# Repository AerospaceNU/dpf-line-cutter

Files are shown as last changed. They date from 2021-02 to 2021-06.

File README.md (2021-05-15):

# Line Cutter: For Cutting Lines
The line cutter is a system for deploying a single parachute as both drogue and main. Reefing lines are used to constrict the parachute to two intermediate sizes, and these lines are threaded through line cutters. At the set altitudes (or after a time delay), nichrome wires burn through the reefing lines.

## Organization
* `code`: Line cutter code and flight data analyses.
  * `launch archive`: Raw flight data and summaries of successes/failures from past line cutter flights. Subfolders should be named with ISO date and launch site.
  * `libraries and drivers`: Should be obsolete soon (drivers etc. will be published as Arduino libraries).
    * `openocd_windows.zip`: Windows build of openOCD with nrf52940 bootloader and cheap st-link config packaged.
  * `tests`: Code that is useful for testing various line cutter features across hardware versions.
  * `v1`: Code for v1 perfboard line cutters.
  * `v2`: Code for mixed perfboard and PCB line cutters.
  * `v3`: Code for current PCB line cutters.
    * `bulk_erase`: Erases all data on flash chip.
    * `flash_reader`: Reads all data on flash chip.
    * `flight_variable_upload`: Sets parameters for flight.
    * `identifier`: Names PCB for Bluetooth advertising.
    * `InternalFS_format`: Erases files on NRF52840 and formats filesystem.
    * `line_cutter_v3`: Main program that runs on flights.
    * `memory_reader`: Reads state transition log.
* `docs`: More detailed documentation, see below for list.
* `schematic`: ECAD files for the line cutter hardware. Contains schematics for all line cutter hardware. Folder structure is described in the [readme](schematic/README.md)

## Documentation
Code documentation applies to the latest version (v1/v2 are not compatible with current line cutters).
* [`CHECKLIST`](docs/CHECKLIST.md): Pre-flight checklist for line cutter launches.
* [`FLASH`](docs/FLASH.md): Procedure for logging data to flash on line cutters.
* [`SIGNALS`](docs/SIGNALS.md): Description of current board.
* [`STATES`](docs/STATES.md): Description of state machine.
* [`nrf52_openocd`](docs/nrf52_openocd.md): Instructions for programming NRF52 chips with OpenOCD.

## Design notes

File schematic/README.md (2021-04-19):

# Line cutter schematics

This folder is organized as follows:
  * `batt-and-reg.cam`: CAM file used for JLC
  * `lineCutterR<N>-.zip`: Production files sent to fab
  * `LineCutter`: eagle project containing all the actual files
    * `Line Cutter COTS.lbr`: common parts used (flash memory, nRF daughterboards, etc)
    * `lineCutterR1`: first PCB ordered (nRF52832, December 2020)
    * `lineCutterR2`: ESP32-S2 based, ordered spring 2021 (1 built, no software written for it)
    * `lineCutterR3`: nRF52840-based, ordered spring 2021. Flew Amesbury 3/20.

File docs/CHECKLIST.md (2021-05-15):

This is the pre-flight checklist that should be followed for every line cutter launch. Detailed instructions for setting up the line cutters are elsewhere; read those first. Consider any time limits mentioned to be a lower bound---completing items *earlier* than the listed time is encouraged, *on-time* is acceptable, and *after* will result in a rushed (read: risky) process. Keep in mind that although the checklist only covers line cutter prep, it implicitly requires that the rest of your rocket is also prepared in a timely manner.

14 days before launch:
- [ ] Ensure that you have all materials needed for setup (if you need to ship more stuff, it's important to know this early)

6 days before launch:
- [ ] Sew outer cases and loops onto your parachute
- [ ] Make a local copy of the `dpf-line-cutter` repository

3 days before launch:
- [ ] Assemble the cases (including nichrome)
- [ ] Decide on reefing amounts and reef the parachute
- [ ] Ejection test with the assembled cases

1 day before launch:
- [ ] Charge all batteries (and spares)
- [ ] Put your PCBs in the cases
- [ ] Erase the flash memory on the PCBs
- [ ] Decide on and upload flight variables
- [ ] Upload flight code

On launch day:
- [ ] Plug in the batteries once you have a reasonable expectation that the PCBs won't run out of memory (< 3 hours before launch)
- [ ] Immediately use `!vars` and `!data` to check for expected values from both line cutters
- [ ] Put (preferably black) etape over LEDs
- [ ] Burrito your parachute and put in your rocket, but don't screw things together yet
- [ ] Use `!data` to check that the photoresistors are reading below ~200 on both line cutters
- [ ] Finish assembling rocket

On the rail:
- [ ] Use `!data` for final confirmation that photoresistors are reading below ~200 and state is `WAITING` on both line cutters
- [ ] Arm both line cutters with `!arm`
- [ ] Use `!data` to confirm that both line cutters are in the `ARMED` state
- [ ] *Optional: if the rocket needs to be taken off the rail for any reason, you should `!disarm` both line cutters and confirm using `!data`*
- [ ] Launch!

After landing:
- [ ] Take photos of both line cutters when you recover your rocket
- [ ] Visually confirm that both lines have disreefed
- [ ] Once you're back at the lab, follow the flash offload instructions to get flight data
- [ ] Send data to the line cutter team
- [ ] Report any potential issues with or damage to the individual line cutters
- [ ] Disassemble and return components

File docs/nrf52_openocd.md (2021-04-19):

# Programming NRF52 chips with OpenOCD

## With ST-Link

St-link V2s can be had for as little as $5, and work on Windows or Linux. A Windows build of OpenOCD, along with config file for the nrf52, is in `code/libraries and drivers/openocd_windows.zip`.

## With a Pi 3ish

Diagrams taken from [here](https://iosoft.blog/2019/01/28/raspberry-pi-openocd/) -- the Medium article went poof but we have the [Internet Archive](https://web.archive.org/web/20191204234928/https://medium.com/@ly.lee/coding-nrf52-with-rust-and-apache-mynewt-on-visual-studio-code-9521bcba6004) for that.

Wire the nRF52 to a Pi 2+ with the following:

```
GND -> GND
SWDIO/TMS -> Physical pin 18 (BCM 24)
SWCLK/TCK -> Physical pin 22 (BCM 25)
nRESET -> Phsyical pin 12
```

Note that the 3v3 rail on the Pi gets sad when you plug a whole Feather in. I'd suggest powering it externally.

Flash a Pi with Raspbian. You'll likely want one with a desktop environment so you can register with Resnet.

Install OpenOCD with `sudo apt update && sudo apt install openocd`

Create a file `bcm-nrf.cfg` with the following:

```
# Use RPi GPIO pins
interface bcm2835gpio

# Base address of I/O port
bcm2835gpio_peripheral_base 0x3F000000

# Clock scaling
bcm2835gpio_speed_coeffs 146203 36

# SWD                swclk swdio
# Header pin numbers 22    18    (counting from 1 on the top left)
bcm2835gpio_swd_nums 25    24

transport select swd

source [find target/nrf52.cfg]

# gdb_breakpoint_override hard
```

Run `sudo openocd -f bcm-nrf.cfg`. This should produce something that looks like this:

```
Open On-Chip Debugger 0.11.0-rc2+dev-00001-g5c17ce508-dirty (2021-01-27-17:38)
Licensed under GNU GPL v2
For bug reports, read
        http://openocd.org/doc/doxygen/bugs.html
DEPRECATED! use 'adapter driver' not 'interface'
Info : Listening on port 6666 for tcl connections
Info : Listening on port 4444 for telnet connections
Info : BCM2835 GPIO JTAG/SWD bitbang driver
Info : clock speed 1001 kHz
Info : SWD DPIDR 0x2ba01477
Info : nrf52.cpu: hardware has 6 breakpoints, 4 watchpoints
Info : starting gdb server for nrf52.cpu on 3333
Info : Listening on port 3333 for gdb connections
```

If you see something that starts with `Error:`, check your connections and try again.

## Flashing Bootloader

Connect with `telnet localhost 4444`. You may need to `sudo apt install telnet` (Linux) or enable the telnet clilent (Windows) first.

We will use the Adafruit bootloader from [here](https://github.com/adafruit/Adafruit_nRF52_Arduino/tree/master/bootloader). A copy is in `code/libraries and drivers/nrf52840_express.hex`. Transfer it to the Pi and run the following command in OpenOCD.

```
reset init
halt
nrf5 mass_erase
program <full/path/to/bootloader.hex> verify
reset
```

Note that you must call `reset` for the board to enumerate. To erase all:

```
nrf52.dap apreg 1 0x04 0x01
nrf52.dap apreg 1 0x04 // This should be 0x01
```

Now the nRF52 can be connected over USB and programmed with the Arduino IDE.

<!-- pi@raspberrypi3:~ $ sudo openocd -f interface/raspberrypi2-native.cfg -c "transport select swd" -f target/nrf52.cfg -d2 -c init -c "reset init" -c halt -c "nrf5 mass_erase" -c "program espruino.hex verify" -c reset -c exit -->

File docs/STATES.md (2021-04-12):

# Line Cutter State Machine

The line cutter uses a simple progression of states. With the exception of the first two states (`waiting` and `armed`), which can be visited multiple times, the states advance in a linear manner.

| State | Requirement | Next state |
|---| --- | --- |
| `waiting` | Receive `!arm` signal from BLE central. | `armed ` |
| `armed` | Receive `!disarm` signal from BLE central. <br> Photoresistor detects bright light.| `waiting` <br> `deployed` |
| `deployed` | Altitude goes below first disreef height. | `partial disreef` |
| `partial disreef` | Altitude goes below second disreef height. | `full disreef` |
| `full disreef` | Speed is below landing limit speed. | `landed` |
| `landed` | N/A | N/A |

## Transitions

All state transitions add data to a state transition log on the NRF52 chip. In addition, some transitions execute special actions first.

* `armed` -> `deployed`: Existing state transition log is deleted.
* `deployed` -> `partial disreef`: PWM begins on first nichrome pin.
* `partial disreef` -> `full disreef`: PWM begins on second nichrome pin.

The PWM on each nichrome pin is started during a state transition, and the time of this transition is marked. Once the defined PWM duration has passed since the transition, the PWM will end.

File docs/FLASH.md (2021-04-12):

# Flash procedure
The line cutter has 16MiB of flash memory divided into 64 sectors of 256kiB each. The first sector is reserved for metadata, including flight variables and a record of which sectors have been written to.

## Writing metadata
Since there are 64 sectors, the first 64 bytes are used to keep track of which sectors are not empty. The rest of the first sector is used for other metadata such as flight information. When a line cutter is turned on, it will use the first 64 bytes to determine the last non-empty sector. Then, it will conduct a linear search of this sector to find the first location with no data, and pick up logging data at that location. When the current sector fills up, the next byte of location metadata is updated. The main advantages of this system are that there are no sector erases (which take ~500ms, or 10 missed data points), and that if a line cutter restarts it is fairly simple to find the first empty flash location.

The line cutter currently logs 64B of data at 20 Hz. At this rate, about 3.5 hours of data can be recorded. After the flash is full, no more data is logged. Leading up to a launch, the flash should be bulk erased before the main program is uploaded, after which the line cutter should be connected to power as little as possible to make sure it doesn't run out of memory.

## Flash contents
| Address (start -> end) | Contents |
| ---| --- |
| 0000000h -> 000003Fh | Whether the corresponding sector is empty. |
| 0000040h -> 003FFFFh | Additional metadata. |
| 0040000h -> 0FFFFFFh | Flight data. |

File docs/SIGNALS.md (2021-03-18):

# Signals

The following signals are connected to the following pins on the nRF module, which correlate to the following Arduino pins on the [Adafruit core](https://github.com/adafruit/Adafruit_nRF52_Arduino/blob/master/variants/feather_nrf52840_express/variant.cpp). Analog pins are listed along with their digital equivilants.

| Description | Physical pin(s) | Arduino pin(s) | Uses | Driver |
| ----- | --- | --- | --- | --- |
| I2c SCL/SDA | P0.11/P0.12 | 22/23 | [Barometer](https://www.digikey.com/en/products/detail/te-connectivity-measurement-specialties/MS560702BA03-50/4700921), [Accelerometer](https://www.digikey.com/en/products/detail/tdk-invensense/ICM-20602/5872870) | Modified MS5xxx, Need to write one |
| SPI MISO/MOSI/SCK/CS0 | P0.15, P0.13, P0.14, P0.16 | 25, 25, 26, 8 | Flash memory | [S25FLx](https://github.com/BleepLabs/S25FLx) |
| SWDIO/SWDCLK | SWDIO/SWDCLK | | Used to program the chip (initially), debugging | |
| BATT_SENSE | P0.02 | A4 (18) | Battery voltage divider | Battery voltage = 2 * (analogRead(A4) / analogReadResolution) |
| CUT_SENSE1/2 | P0.03/0.04 | A5/A0 (19/14)  | Nichrome continuity | Should read about half of Vbatt when connected |
| V_CURR_SENSE | P0.05 | A1 (15) | [Current sense IC](https://www.digikey.com/en/products/detail/allegro-microsystems/ACS711KEXLT-15AB-T/3868192) | The output rises by 90mV / Amp, centered around VCC/2. We should figure out how to read Vcc |
| PHOTO- | P0.28 | A3 (17) | Output of the photoresistor voltage divider |
| CUT1/2 | P0.06/0.08 | 11, 12 | MOSFETs for nichrome |
| RESET | P0.18 | Not Usable | Reset button |
| UART RXD/TXD | P0.24/P0.25 | 1, 0 | UART (Not used currently) |
| USER LED | P1.10 | 4 (PIN_LED2) | Lefmost LED ("blue" LED on feathers). By default blinks for Bluetooth connection |
| RGB LED | P0.17, P0.19, P0.20 | 29, 27, 28 | Red, Green, Blue, respectively |

# Things to check before plugging a board in

- Resistance between ground and:
  - 3v3 (header)
  - VBUS (from the USB, header)
  - VBAT
  - SCL/SDA (should be open -- short will cause sketch to hang)

- Resistance between 3v3 and:
  - SCL/SDA (4.7k pullup expected)

# Places to watch out for

- Accelerometer -- Can't see shorts
- nRF -- can't see solder joints, and reflowing after oven will likely kill it

# Board names

| Board Number | Name | Known Issues |
| ----- | --- | --- |
| 1 | 0Strawberry | |
| 2 | 0Cherry | |
| 3 | 0Did you ever hear the tragedy of Darth Plagueis the Wise? | |
| 4 | 0Apple | |

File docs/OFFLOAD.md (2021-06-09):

# Summary
This document explains how to offload data from the line cutters' flash memory. It will also go over proper folder organization for commits of data to the repository.

# Setup
You should already have a local version of this repo as part of the general preparation for a line cutter flight. In addition, download [CoolTerm](https://freeware.the-meiers.org/), which will be used to save data from the Arduino serial monitor.

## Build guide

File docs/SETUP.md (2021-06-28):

# Line Cutter Setup
blah blah
## Table of Contents
- Materials
- Sew cases and loops
- Assemble cases (with nichrome and PCBs)
- Choose reefing diameters and flight variables
- Upload code
- Use BluefruitConnect
- Pack the parachute
- Steps after launch

## Materials
- 2 line cutter PCBs
- 2 line cutter cases
- 2-56 screws
	- 6 x 1/2"
	- 8 x 3/16" (1/8" works but pain)
	- 4 x 1/4"
- [0.1" diameter music wire](https://www.mcmaster.com/8908K91/)
- [0.8mm spectra](https://www.amazon.com/dp/B0829L71KC/ref=twister_B07DPGJK3L?th=1&psc=1). Don't use 0.5mm.
- [28 gauge nichrome wire](https://www.amazon.com/Nichrome-80-Gauge-Resistance-Wire/dp/B07CHTT73J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)
- whatever's used to sew it on
- big needle
- Parachute
- BluefruitConnect app (available on iOS and Android)
- 3 380mAh LiPos ?
- LiPo charger
- Micro USB cable
- GoPro if you want style points

## Sew cases and loops
- Before you start, install the springy tabs in the bottom of the cases with two #4-40 x 1/4" screws
- Two line cutter cases should be sewn on to the throat of the parachute. They should be situated on opposite sides of the parachute (180º apart). Each case should be sewn to the inside of the chute at a point where one of the shrouds attaches. The longest dimension of the case should be in the direction of the shroud. The two cases should be situated head-to-tail. That is, if you start at the hinged face of one case and travel around the throat of the parachute to the other case in the direction that does not require you to cross through the first case, you should arrive at the second case on its non-hinged side. Use a thick embroidery needle and Delrin string.

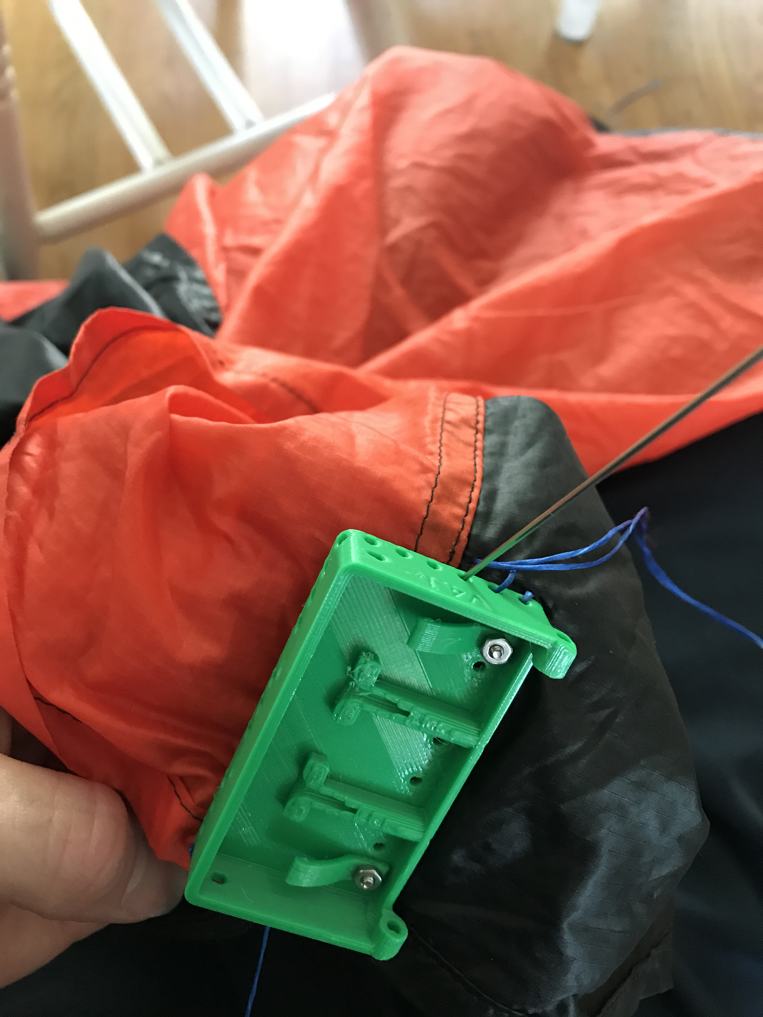
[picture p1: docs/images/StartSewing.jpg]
start sewing


- Back each case with a piece of felt to serve as protective batting. The felt will help prevent damage to the thin nylon that the parachute is made of. On the outer face of the parachute it should look something like this:

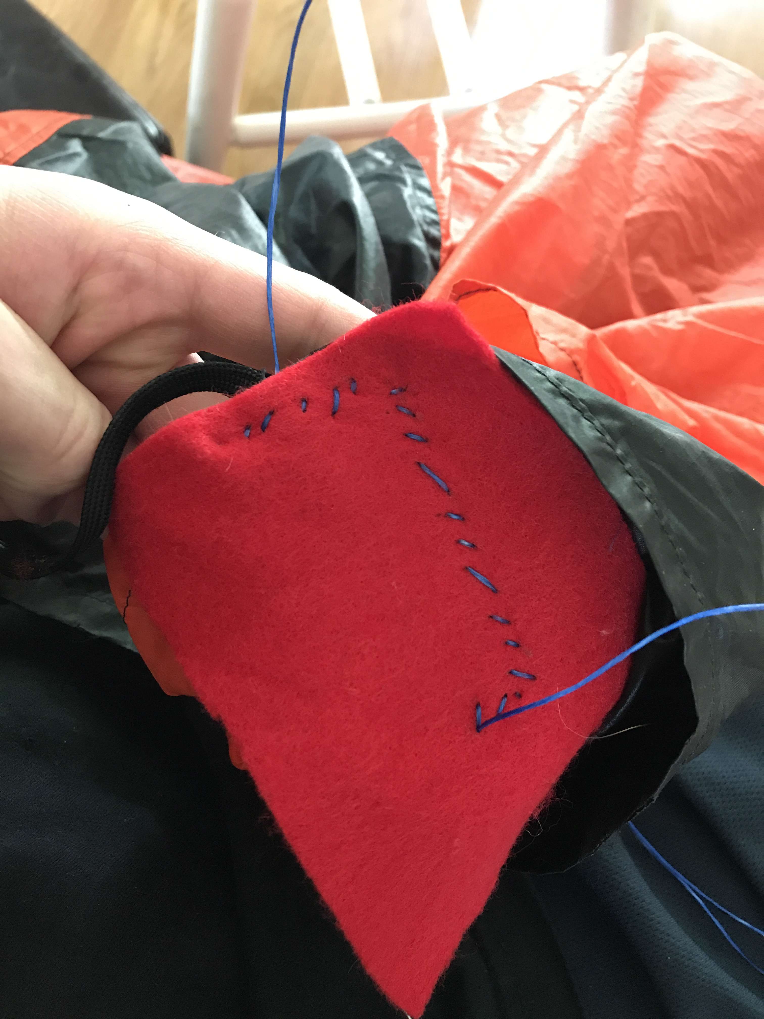
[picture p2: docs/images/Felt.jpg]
felt batting


And on the inner face, it should look like this:

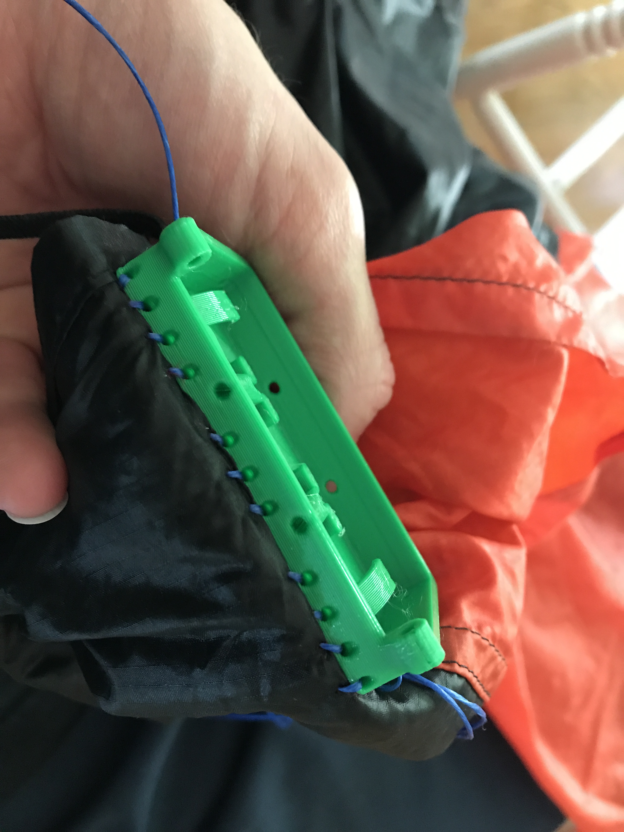
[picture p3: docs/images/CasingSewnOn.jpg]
sew on case


- When you are done, cut away the excess felt from the other side:

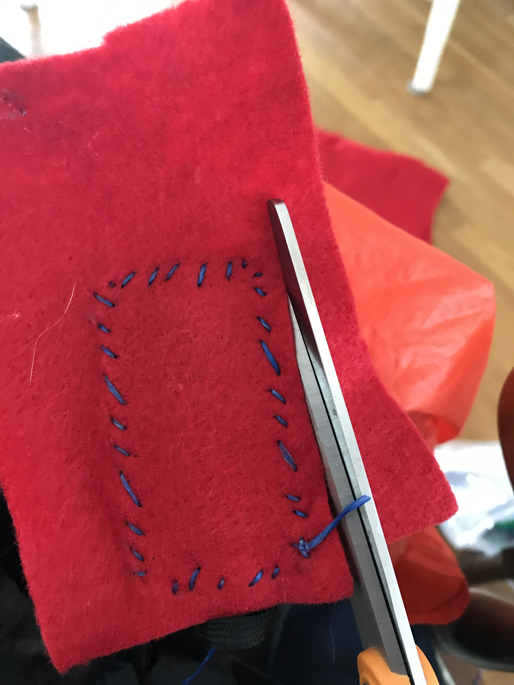
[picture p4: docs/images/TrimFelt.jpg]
felt trimming


So you end up with this:

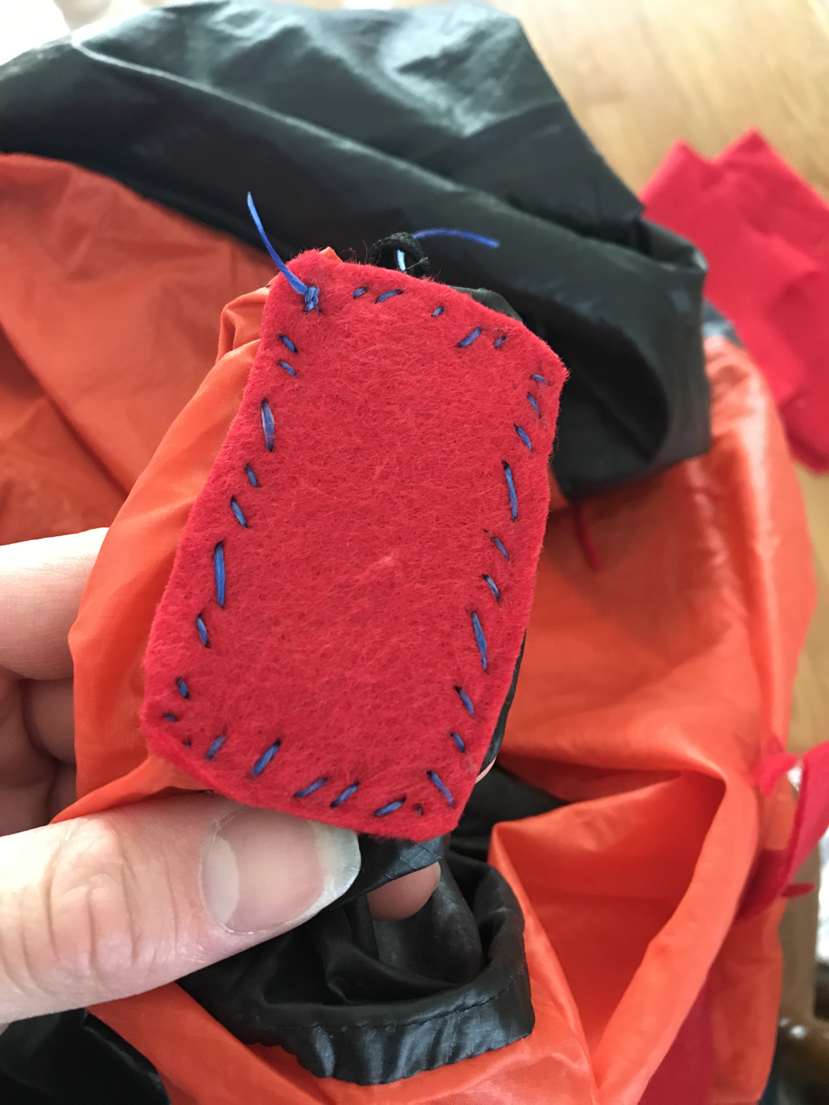
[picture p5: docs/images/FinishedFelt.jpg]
felt finished


## Assemble cases (with nichrome and PCBs)
- If you haven't already, insert long-style 4-40 heat set inserts into the three screw holes on the bottom of the rocker. Also insert the heat sets needed to secure the batter cover. In the picture below, there are heat sets underneath each of the screw heads shown. For the nichrome attachment screws, the heat sets should sit flush with the bottom face of the rocker. After that, install the nichrome wire with three 3/16" screws (I think that's the size we used). A washer should go above and below the wire on each screw. The wire should be pulled relatively tight because it will expand significantly when heated. Wrap the wire around each screw once, starting with the left screw and tightening each screw as you go. The nichrome should be aligned on the side of the screws closer to the face of the rocker marked with the date and the version.

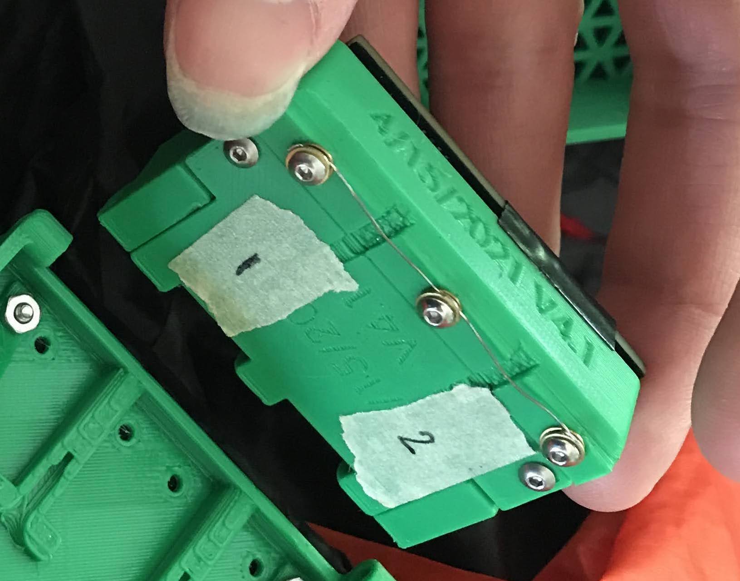
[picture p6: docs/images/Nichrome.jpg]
Nichrome Installation


- Screw on the battery cover.
- Install short 4-40 heat sets in the tabs extending from the bottom of the casing cover:

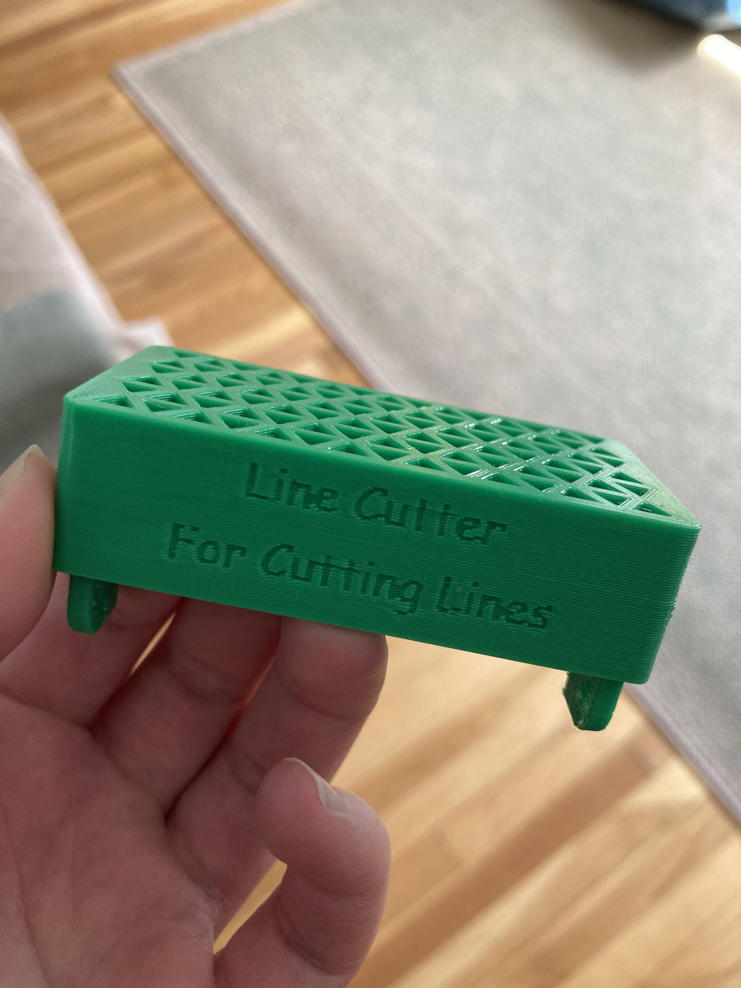
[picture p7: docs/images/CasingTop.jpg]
Casing Top


Like so:

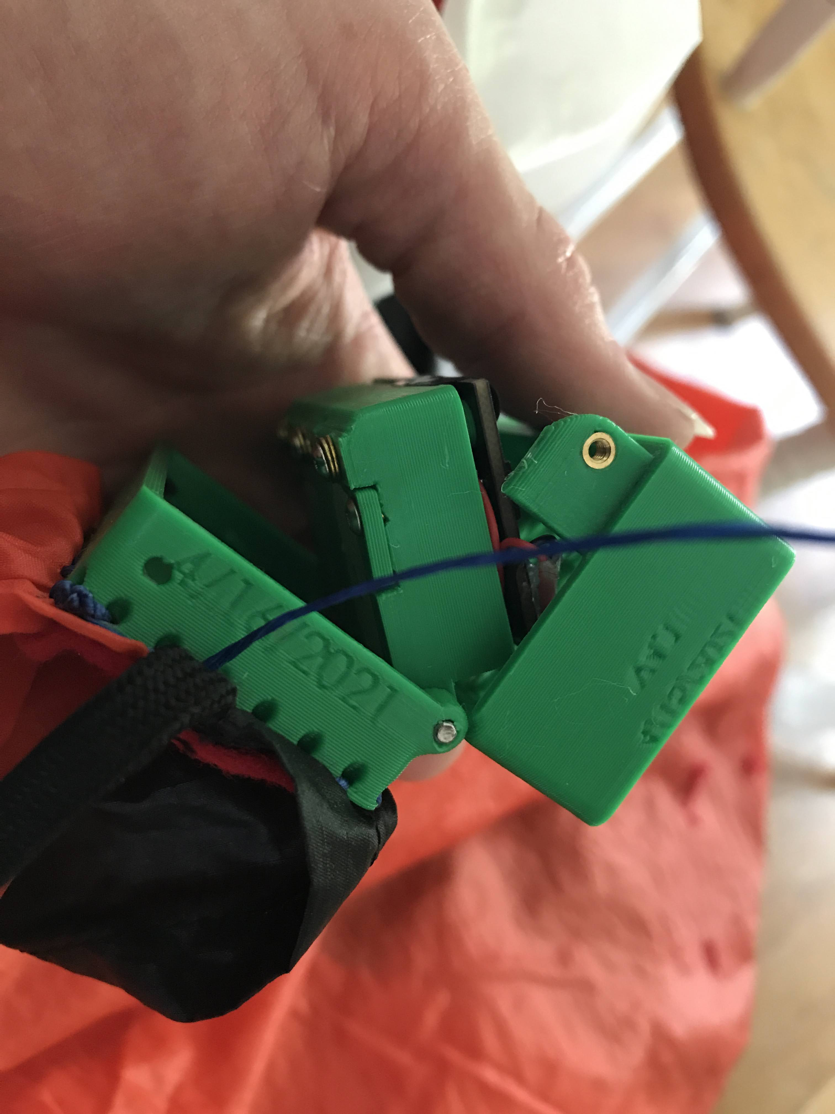
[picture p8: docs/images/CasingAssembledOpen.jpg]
Assembled Case Open


- Then run a 0.1" diameter music wire hinge pin through the hinge holes on all the casing components to hold the entire case together, as shown in the previous picture

- Sew on double-thick Delrin loops at the point where each of the shrouds attaches to the parachute, except for the attachment points where the line cutters have already been sewn on. The loops should be around 1" in diameter and should pierce the shroud line, or at the very least pass around it (so that the reefing line will tug on the shroud, not just the fabric of the chute). Tie them closed with multiple square knots and put a dab of super glue on the knots.

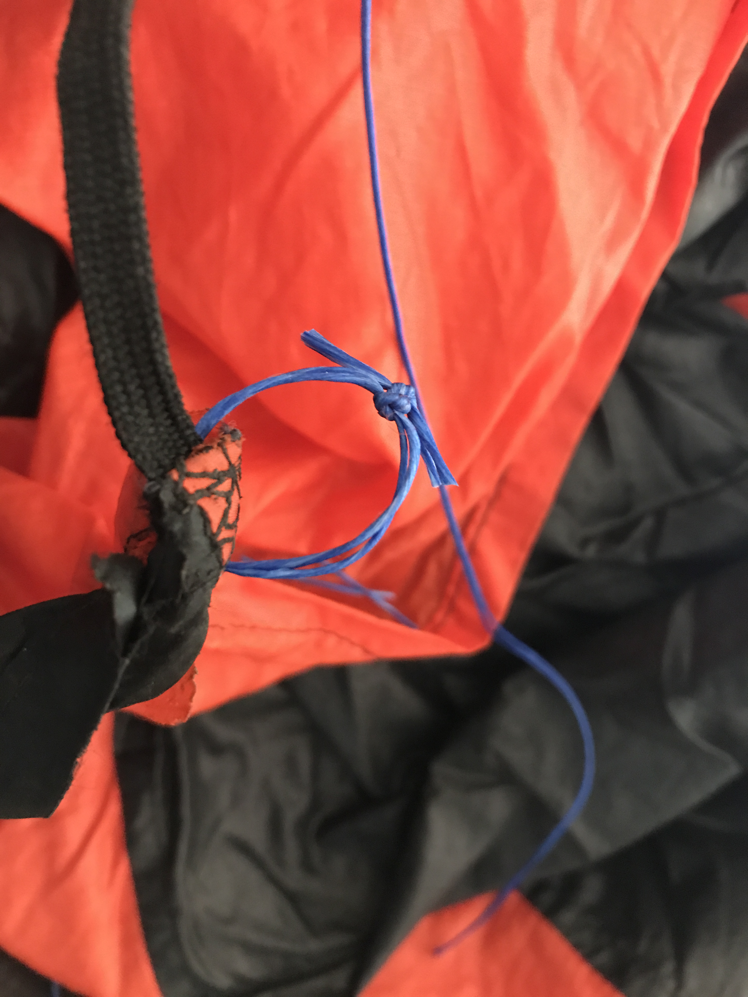
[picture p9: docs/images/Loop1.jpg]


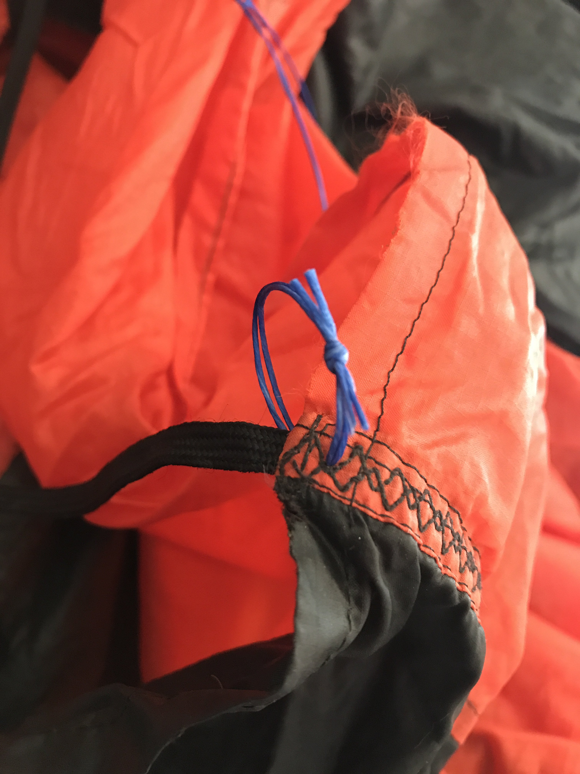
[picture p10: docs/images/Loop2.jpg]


## Choose reefing diameters and flight variables
## Upload code
## Use BluefruitConnect
## Pack the parachute
## Steps after launch

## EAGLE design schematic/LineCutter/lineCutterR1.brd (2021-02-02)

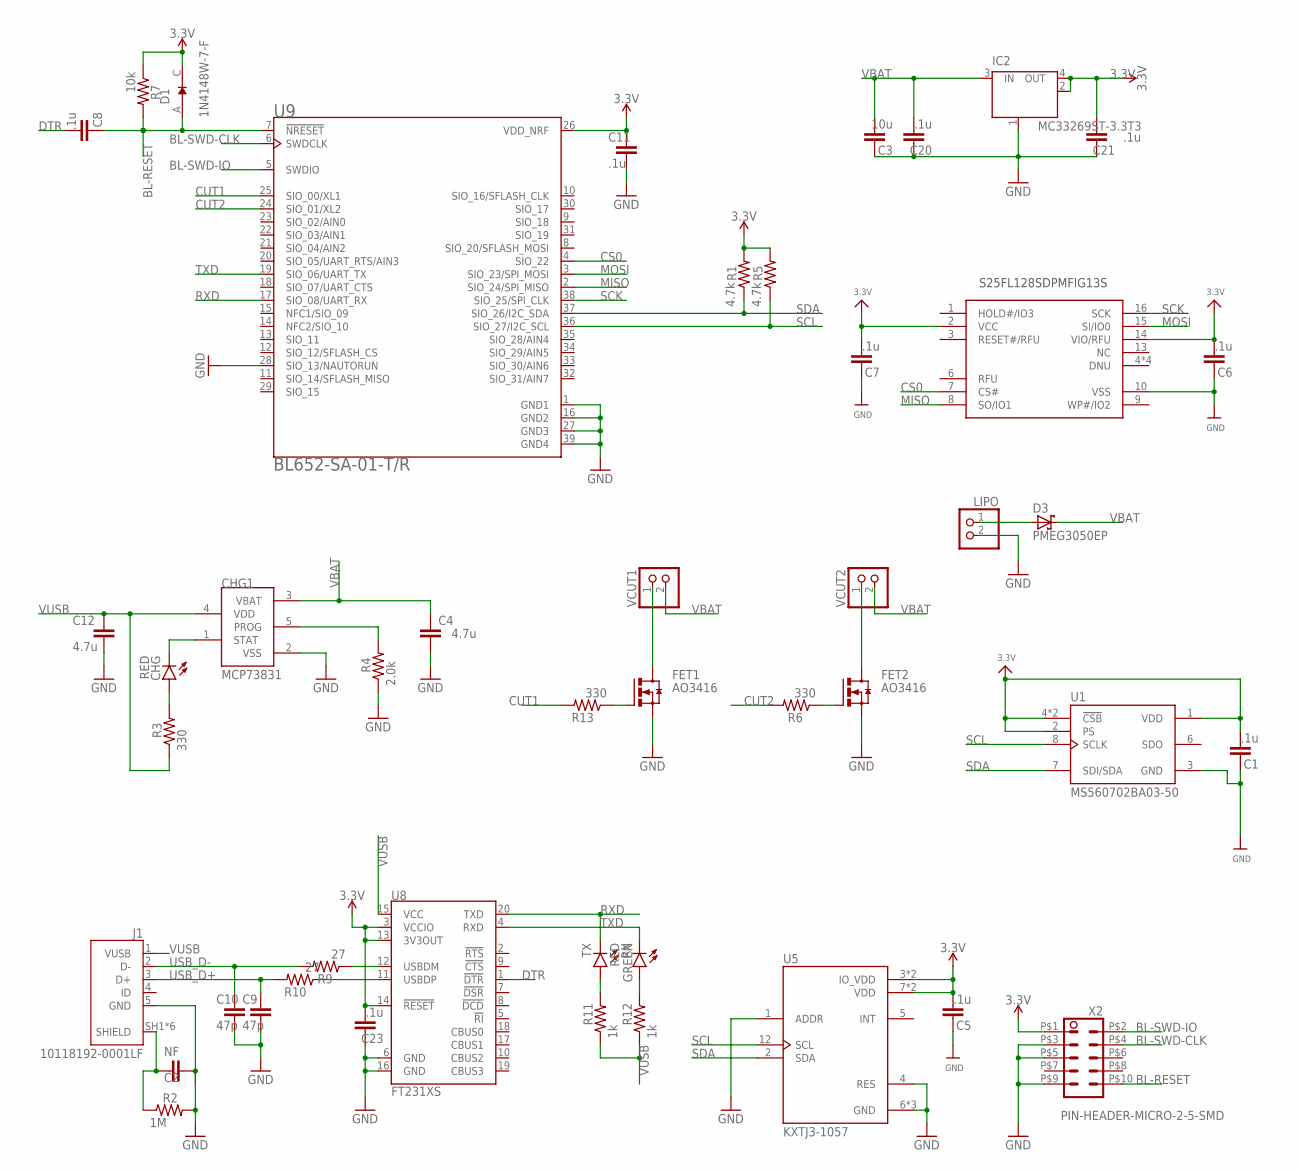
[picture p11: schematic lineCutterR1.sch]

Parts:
C1, C5, C6, C7, C8, C11, C20, C21, C23: .1u; C0805
C2: NF; C0805
C3: 10u; C0805
C4, C12: 4.7u; C0805
C9, C10: 47p; C0805
CHG: RED; CHIP-LED0805
CHG1: MCP73831; SOT23-5L
D1: 1N4148W-7-F; SOD3715X135N
D3: PMEG3050EP; SOD128
FET1, FET2: AO3416; SOT23-3
IC2: MC33269ST-3.3T3; SOT223
J1: 10118192-0001LF; AMPHENOL_10118192-0001LF
LIPO: PINHD-1X2; 1X02
R1, R5: 4.7k; R0805
R2: 1M; R0805
R3, R6, R13: 330; R0805
R4: 2.0k; R0805
R7: 10k; R0805
R9, R10: 27; R0805
R11, R12: 1k; R0805
RX: RED; CHIP-LED0805
TX: GREEN; CHIP-LED0805
U1: MS560702BA03-50; SON125P300X500X100-8N
U3: S25FL128SDPMFIG13S03016; SOIC127P1032X265-16N
U5: KXTJ3-1057; KIONIX_KXTJ3-1057
U8: FT231XS; SSOP20_L
U9: BL652-SA-01-T/R; XCVR_BL652-SA-01-T/R
VCUT1, VCUT2: PINHD-1X2; 1X02
X2: PIN-HEADER-MICRO-2-5-SMD; PIN-HEADER-NICRO-2-5-SMD

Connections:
3.3V: C1.2, C5.2, C6.2, C7.2, C11.1, C21.2, C23.2, D1.C (K), IC2.2 (OUT), IC2.4 (OUT), R1.2, R5.2, R7.1, U1.1 (VDD), U1.2 (PS), U1.4 (!CSB), U1.5 (!CSB), U3.2 (VCC), U3.14 (VIO/RFU), U5.3 (IO_VDD), U5.7 (VDD), U5.10 (VDD), U5.11 (IO_VDD), U8.3 (VCCIO), U8.13 (3V3OUT), U8.14 (!RESET), U9.26 (VDD_NRF), X2.P$1 (1)
BL-RESET: C8.1, D1.A, R7.2, U9.7 (!NRESET), X2.P$10 (10)
BL-SWD-CLK: U9.6 (SWDCLK), X2.P$4 (4)
BL-SWD-IO: U9.5 (SWDIO), X2.P$2 (2)
CS0: U3.7 (CS#), U9.4 (SIO_22)
CUT1: R13.2, U9.25 (SIO_00/XL1)
CUT2: R6.2, U9.24 (SIO_01/XL2)
DTR: C8.2, U8.1 (!DTR)
GND: C1.1, C2.1, C3.1, C4.2, C5.1, C6.1, C7.1, C9.2, C10.2, C11.2, C12.2, C20.1, C21.1, C23.1, CHG1.2 (VSS), FET1.2 (S), FET2.2 (S), IC2.1 (GND/ADJ), J1.5 (GND), LIPO.2, R2.2, R4.1, U1.3 (GND), U3.10 (VSS), U5.1 (ADDR), U5.4 (RES), U5.6 (GND), U5.8 (GND), U5.9 (GND), U8.6 (GND), U8.16 (GND), U9.1 (GND1), U9.16 (GND2), U9.27 (GND3), U9.28 (SIO_13/NAUTORUN), U9.39 (GND4), X2.P$3 (3), X2.P$5 (5), X2.P$9 (9)
MISO: U3.8 (SO/IO1), U9.2 (SIO_24/SPI_MISO)
MOSI: U3.15 (SI/IO0), U9.3 (SIO_23/SPI_MOSI)
unnamed: CHG.A, R3.2
unnamed: C2.2, J1.SH1 (SHIELD), J1.SH2 (SHIELD), J1.SH3 (SHIELD), J1.SH4 (SHIELD), J1.SH5 (SHIELD), J1.SH6 (SHIELD), R2.1
unnamed: FET2.1 (G), R6.1
unnamed: CHG1.5 (PROG), R4.2
unnamed: CHG.C, CHG1.1 (STAT)
unnamed: FET2.3 (D), VCUT2.1
unnamed: D3.2 (A), LIPO.1
unnamed: FET1.1 (G), R13.1
unnamed: R9.1, U8.12 (USBDM)
unnamed: R10.1, U8.11 (USBDP)
unnamed: FET1.3 (D), VCUT1.1
unnamed: R11.2, TX.A
unnamed: R12.2, RX.A
RXD: TX.C, U8.20 (TXD), U9.17 (SIO_08/UART_RX)
SCK: U3.16 (SCK), U9.38 (SIO_25/SPI_CLK)
SCL: R5.1, U1.8 (SCLK), U5.12 (SCL), U9.36 (SIO_27/I2C_SCL)
SDA: R1.1, U1.7 (SDI/SDA), U5.2 (SDA), U9.37 (SIO_26/I2C_SDA)
TXD: RX.C, U8.4 (RXD), U9.19 (SIO_06/UART_TX)
USB_D+: C9.1, J1.3 (D+), R10.2
USB_D-: C10.1, J1.2 (D-), R9.2
VBAT: C3.2, C4.1, C20.2, CHG1.3 (VBAT), D3.1 (K), IC2.3 (IN), VCUT1.2, VCUT2.2
VUSB: C12.1, CHG1.4 (VDD), J1.1 (VUSB), R3.1, R11.1, R12.1, U8.15 (VCC)

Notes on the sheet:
S25FL128SDPMFIG13S

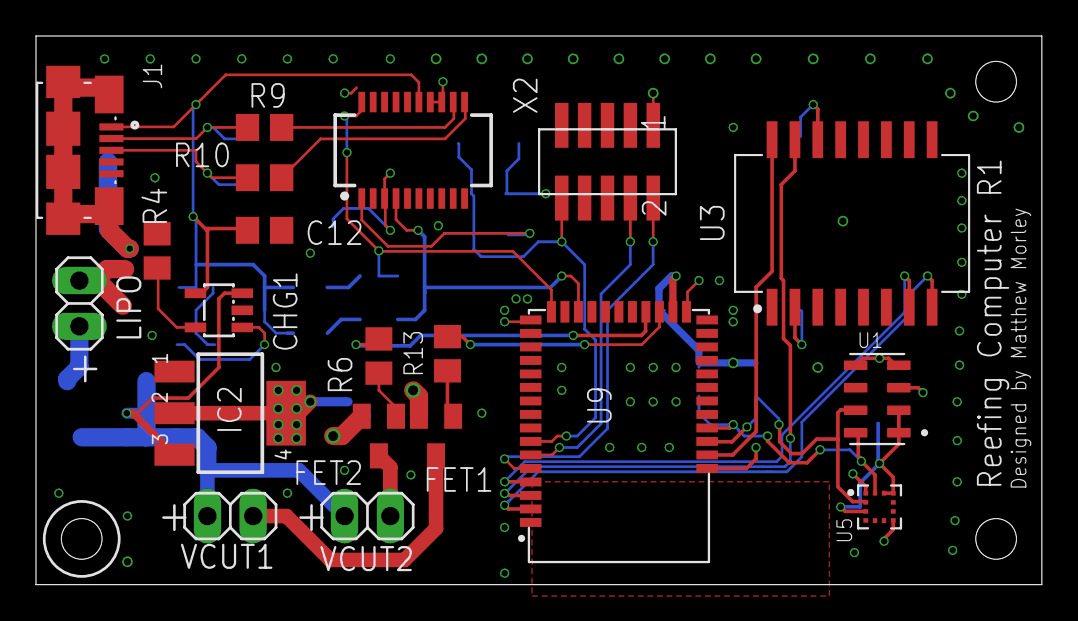
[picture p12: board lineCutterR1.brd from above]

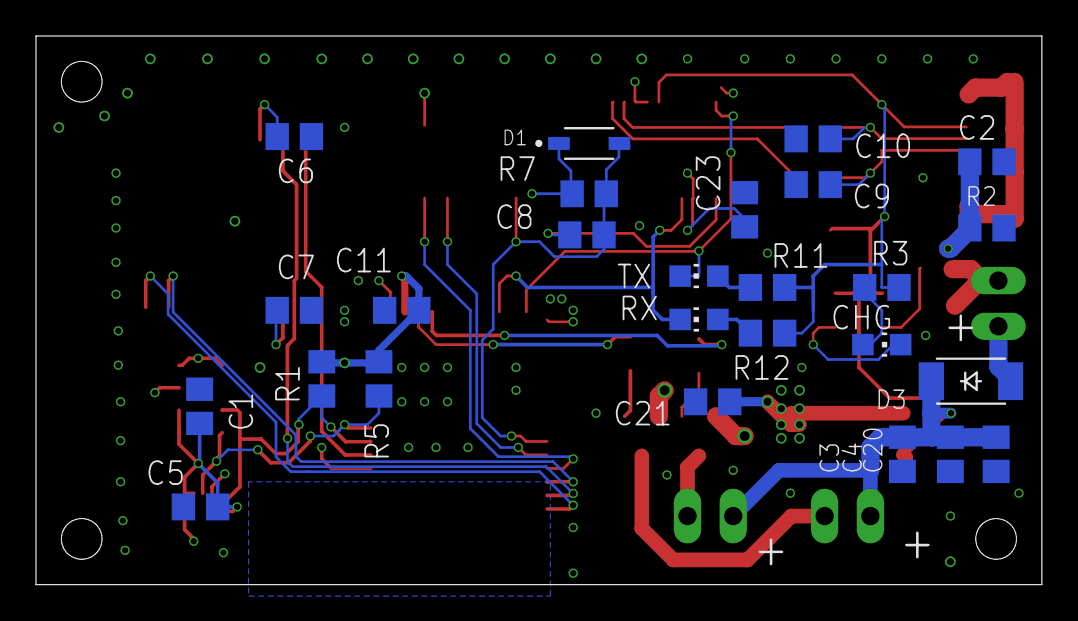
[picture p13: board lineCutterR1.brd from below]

Board: 4 copper layers, 55.9 x 30.5 mm, 46 parts (26 on the bottom side), 33 nets.

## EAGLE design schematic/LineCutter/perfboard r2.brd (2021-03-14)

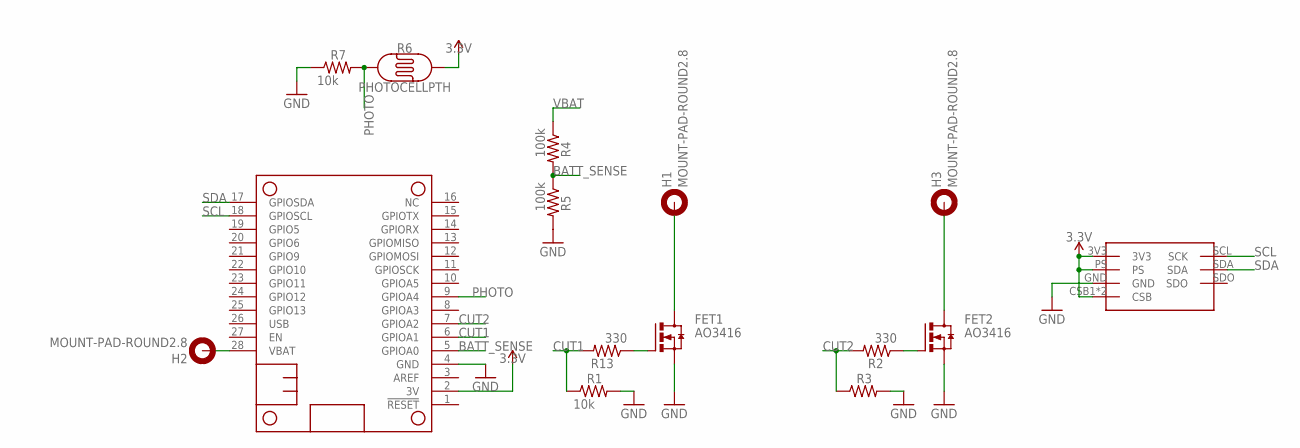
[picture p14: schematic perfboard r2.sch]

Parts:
FET1, FET2: AO3416; SOT23-3
H1, H2, H3: MOUNT-PAD-ROUND2.8; 2,8-PAD
MS1: FEATHERWING_NODIM
R1, R3, R7: 10k; 0204/7
R2, R13: 330; 0204/7
R4, R5: 100k; 0204/7
R6: PHOTOCELLPTH; PHOTOCELL
U$1: MS5607_BREAKOUT; MS5607BREAKOUT

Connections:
3.3V: MS1.2 (3V), R6.2, U$1.3V3, U$1.CSB1 (CSB), U$1.CSB2 (CSB), U$1.PS
BATT_SENSE: MS1.5 (GPIOA0), R4.2, R5.1
CUT1: MS1.6 (GPIOA1), R1.1, R13.2
CUT2: MS1.7 (GPIOA2), R2.2, R3.1
GND: FET1.2 (S), FET2.2 (S), MS1.4 (GND), R1.2, R3.2, R5.2, R7.1, U$1.GND
unnamed: FET1.3 (D), H1.B2,8
unnamed: FET2.1 (G), R2.1
unnamed: FET2.3 (D), H3.B2,8
unnamed: FET1.1 (G), R13.1
PHOTO: MS1.9 (GPIOA4), R6.1, R7.2
SCL: MS1.18 (GPIOSCL), U$1.SCL (SCK)
SDA: MS1.17 (GPIOSDA), U$1.SDA
VBAT: H2.B2,8, MS1.28 (VBAT), R4.1

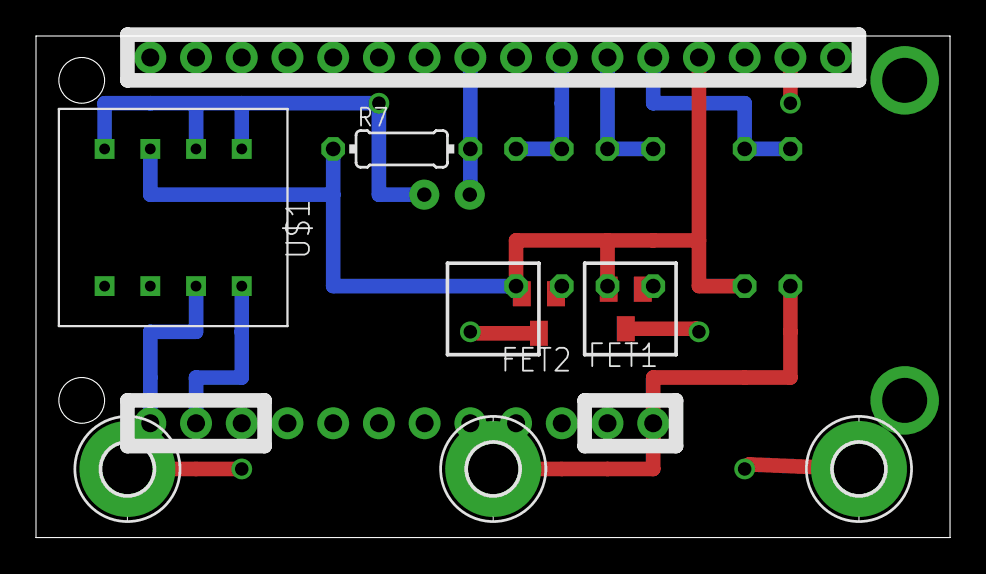
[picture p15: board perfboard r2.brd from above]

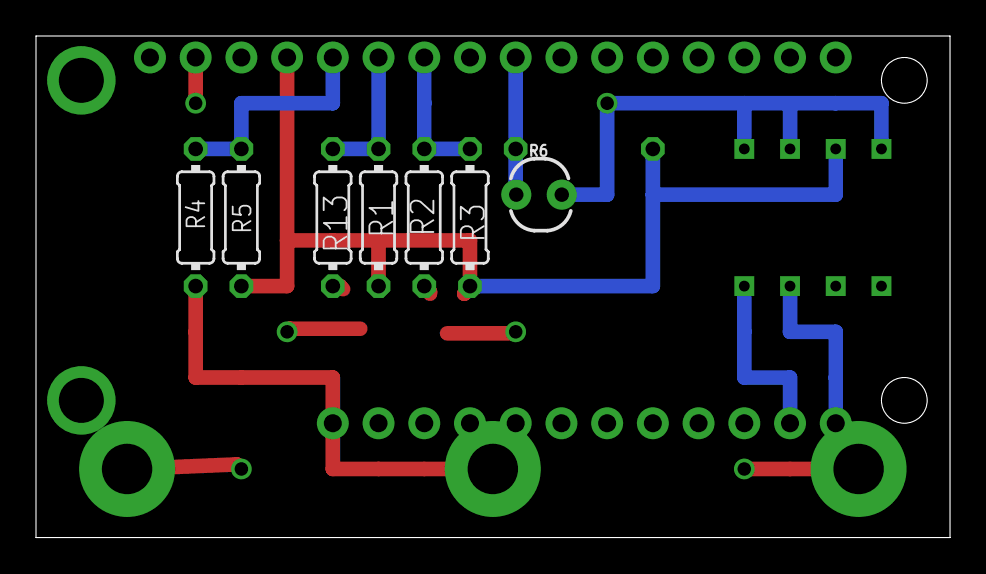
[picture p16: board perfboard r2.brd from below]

Board: 4 copper layers, 50.8 x 27.9 mm, 16 parts (7 on the bottom side), 13 nets.

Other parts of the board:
U$14: NRF52840_TOP

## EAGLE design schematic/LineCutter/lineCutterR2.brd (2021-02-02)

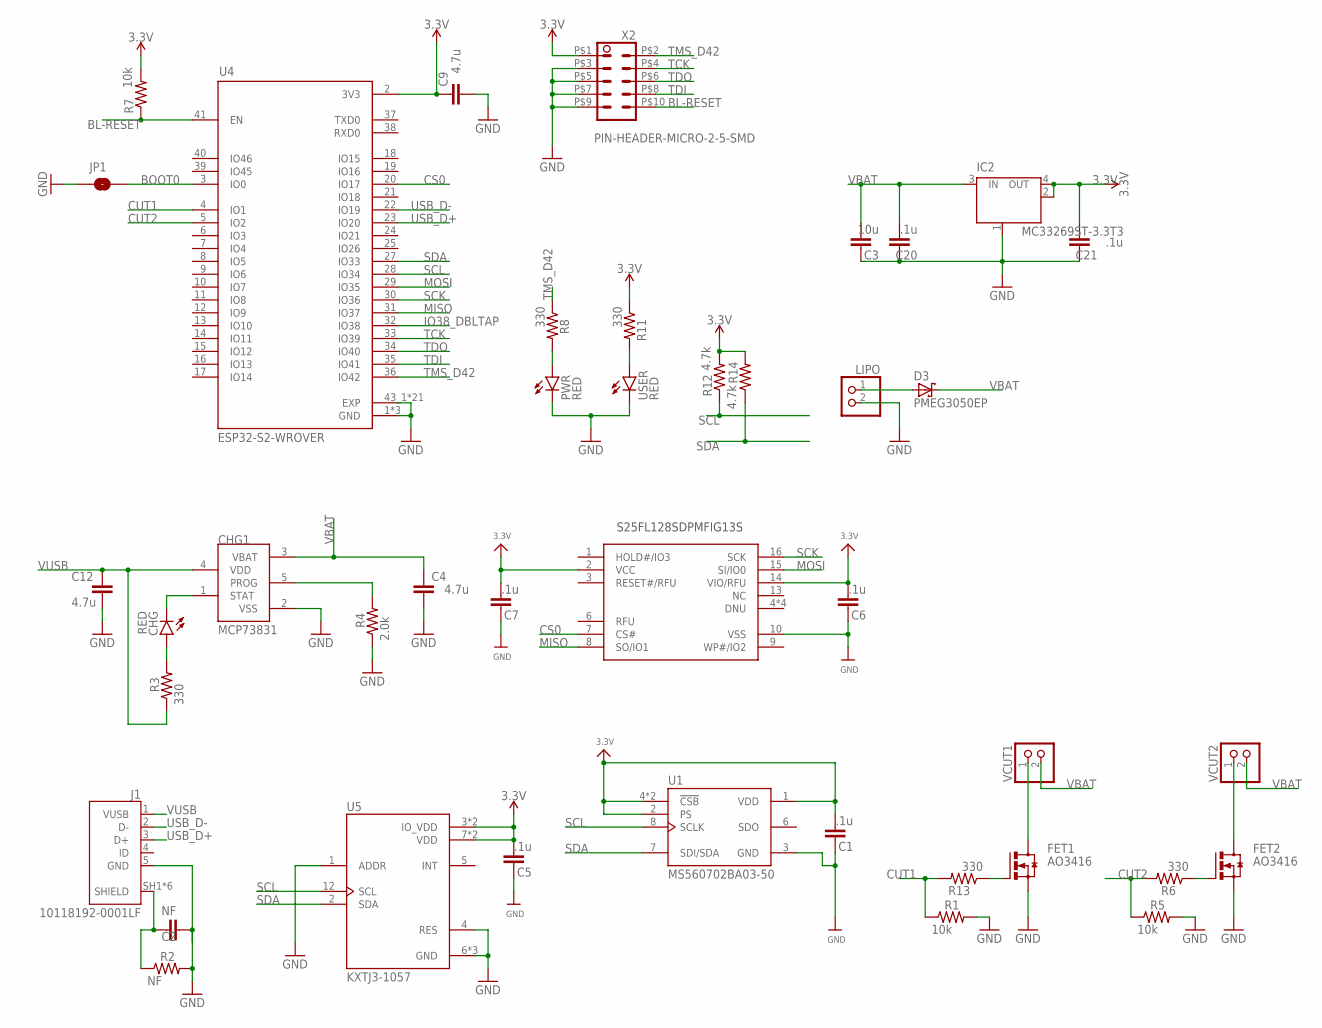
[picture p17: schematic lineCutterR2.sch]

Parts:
C1, C5, C6, C7, C20, C21: .1u; C0805
C2: NF; C0805
C3: 10u; C0805
C4, C9, C12: 4.7u; C0805
CHG: RED; CHIP-LED0805
CHG1: MCP73831; SOT23-5L
D3: PMEG3050EP; SOD128
FET1, FET2: AO3416; SOT23-3
IC2: MC33269ST-3.3T3; SOT223
J1: 10118192-0001LF; AMPHENOL_10118192-0001LF
JP1: JUMPER-SMT_2_NO_SILK; SMT-JUMPER_2_NO_SILK
LIPO: PINHD-1X2; 1X02
PWR: RED; CHIP-LED0805
R1, R5, R7: 10k; R0805
R2: NF; R0805
R3, R6, R8, R11, R13: 330; R0805
R4: 2.0k; R0805
R12, R14: 4.7k; R0805
U1: MS560702BA03-50; SON125P300X500X100-8N
U3: S25FL128SDPMFIG13S03016; SOIC127P1032X265-16N
U4: ESP32-S2-WROVER; MODULE_ESP32-S2-WROVER
U5: KXTJ3-1057; KIONIX_KXTJ3-1057
USER: RED; CHIP-LED0805
VCUT1, VCUT2: PINHD-1X2; 1X02
X2: PIN-HEADER-MICRO-2-5-SMD; PIN-HEADER-NICRO-2-5-SMD

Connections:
3.3V: C1.2, C5.2, C6.2, C7.2, C9.1, C21.2, IC2.2 (OUT), IC2.4 (OUT), R7.2, R11.1, R12.2, R14.2, U1.1 (VDD), U1.2 (PS), U1.4 (!CSB), U1.5 (!CSB), U3.2 (VCC), U3.14 (VIO/RFU), U4.2 (3V3), U5.3 (IO_VDD), U5.7 (VDD), U5.10 (VDD), U5.11 (IO_VDD), X2.P$1 (1)
BL-RESET: R7.1, U4.41 (EN), X2.P$10 (10)
BOOT0: JP1.2, U4.3 (IO0)
CS0: U3.7 (CS#), U4.20 (IO17)
CUT1: R1.1, R13.2, U4.4 (IO1)
CUT2: R5.1, R6.2, U4.5 (IO2)
GND: C1.1, C2.1, C3.1, C4.2, C5.1, C6.1, C7.1, C9.2, C12.2, C20.1, C21.1, CHG1.2 (VSS), FET1.2 (S), FET2.2 (S), IC2.1 (GND/ADJ), J1.5 (GND), JP1.1, LIPO.2, PWR.C, R1.2, R2.2, R4.1, R5.2, U1.3 (GND), U3.10 (VSS), U4.1 (GND), U4.26 (GND), U4.42 (GND), U4.43_1 (EXP), U4.43_2 (EXP), U4.43_3 (EXP), U4.43_4 (EXP), U4.43_5 (EXP), U4.43_6 (EXP), U4.43_7 (EXP), U4.43_8 (EXP), U4.43_9 (EXP), U4.43_10 (EXP), U4.43_11 (EXP), U4.43_12 (EXP), U4.43_13 (EXP), U4.43_14 (EXP), U4.43_15 (EXP), U4.43_16 (EXP), U4.43_17 (EXP), U4.43_18 (EXP), U4.43_19 (EXP), U4.43_20 (EXP), U4.43_21 (EXP), U5.1 (ADDR), U5.4 (RES), U5.6 (GND), U5.8 (GND), U5.9 (GND), USER.C, X2.P$3 (3), X2.P$5 (5), X2.P$7 (7), X2.P$9 (9)
IO38_DBLTAP: U4.32 (IO38)
MISO: U3.8 (SO/IO1), U4.31 (IO37)
MOSI: U3.15 (SI/IO0), U4.29 (IO35)
unnamed: CHG.A, R3.2
unnamed: C2.2, J1.SH1 (SHIELD), J1.SH2 (SHIELD), J1.SH3 (SHIELD), J1.SH4 (SHIELD), J1.SH5 (SHIELD), J1.SH6 (SHIELD), R2.1
unnamed: FET2.1 (G), R6.1
unnamed: CHG1.5 (PROG), R4.2
unnamed: CHG.C, CHG1.1 (STAT)
unnamed: FET2.3 (D), VCUT2.1
unnamed: PWR.A, R8.2
unnamed: D3.2 (A), LIPO.1
unnamed: R11.2, USER.A
unnamed: FET1.1 (G), R13.1
unnamed: FET1.3 (D), VCUT1.1
SCK: U3.16 (SCK), U4.30 (IO36)
SCL: R12.1, U1.8 (SCLK), U4.28 (IO34), U5.12 (SCL)
SDA: R14.1, U1.7 (SDI/SDA), U4.27 (IO33), U5.2 (SDA)
TCK: U4.33 (IO39), X2.P$4 (4)
TDI: U4.35 (IO41), X2.P$8 (8)
TDO: U4.34 (IO40), X2.P$6 (6)
TMS_D42: R8.1, U4.36 (IO42), X2.P$2 (2)
USB_D+: J1.3 (D+), U4.23 (IO20)
USB_D-: J1.2 (D-), U4.22 (IO19)
VBAT: C3.2, C4.1, C20.2, CHG1.3 (VBAT), D3.1 (K), IC2.3 (IN), VCUT1.2, VCUT2.2
VUSB: C12.1, CHG1.4 (VDD), J1.1 (VUSB), R3.1

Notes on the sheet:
S25FL128SDPMFIG13S

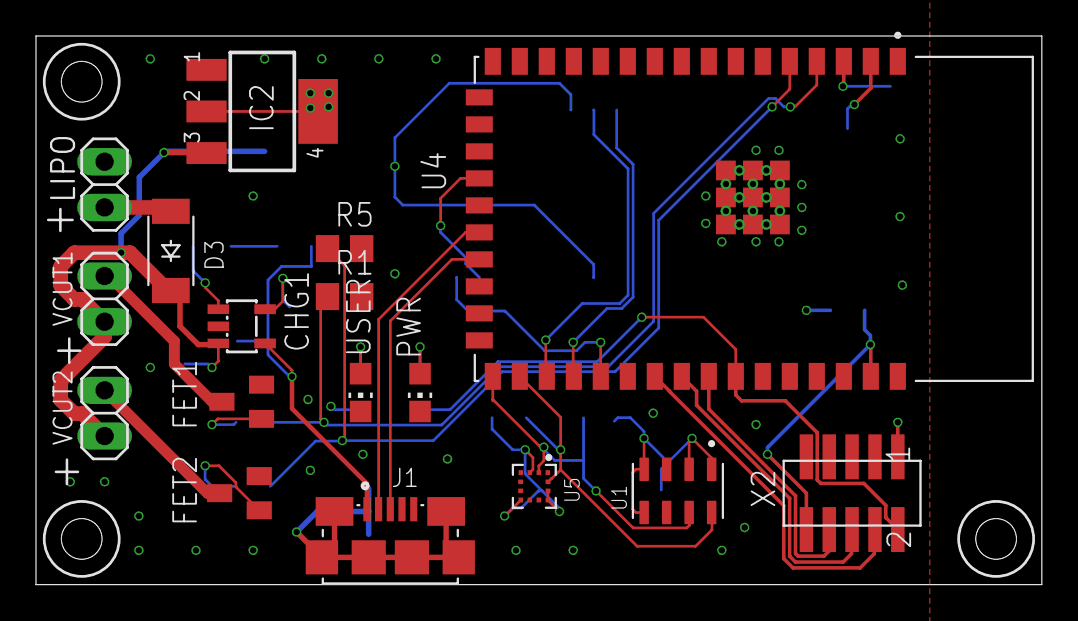
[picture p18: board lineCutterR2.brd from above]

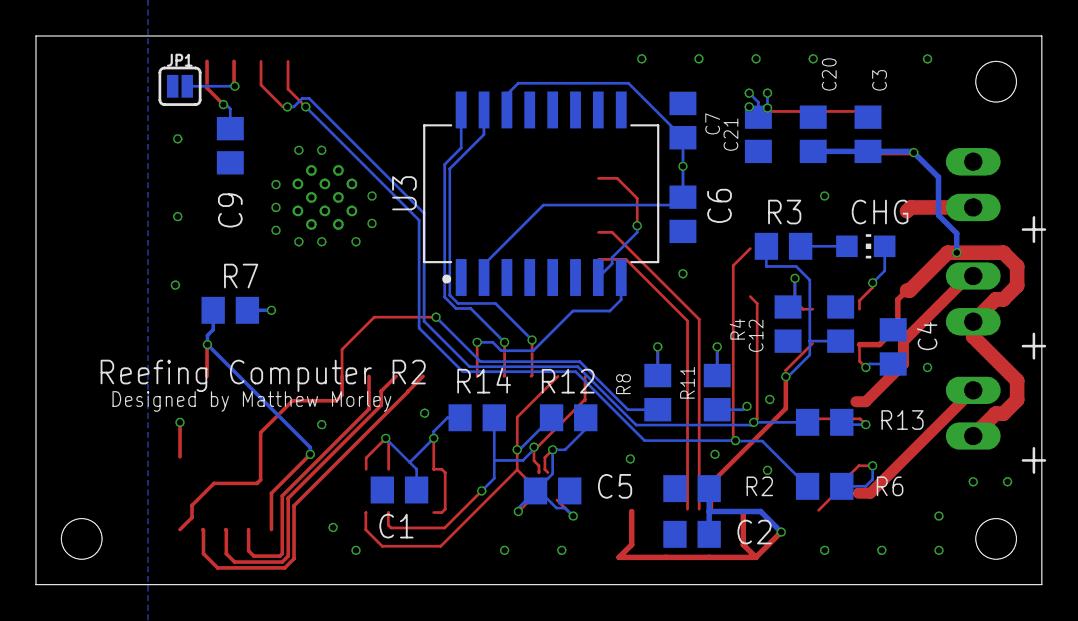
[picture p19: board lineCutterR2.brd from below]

Board: 4 copper layers, 55.9 x 30.5 mm, 41 parts (24 on the bottom side), 31 nets.

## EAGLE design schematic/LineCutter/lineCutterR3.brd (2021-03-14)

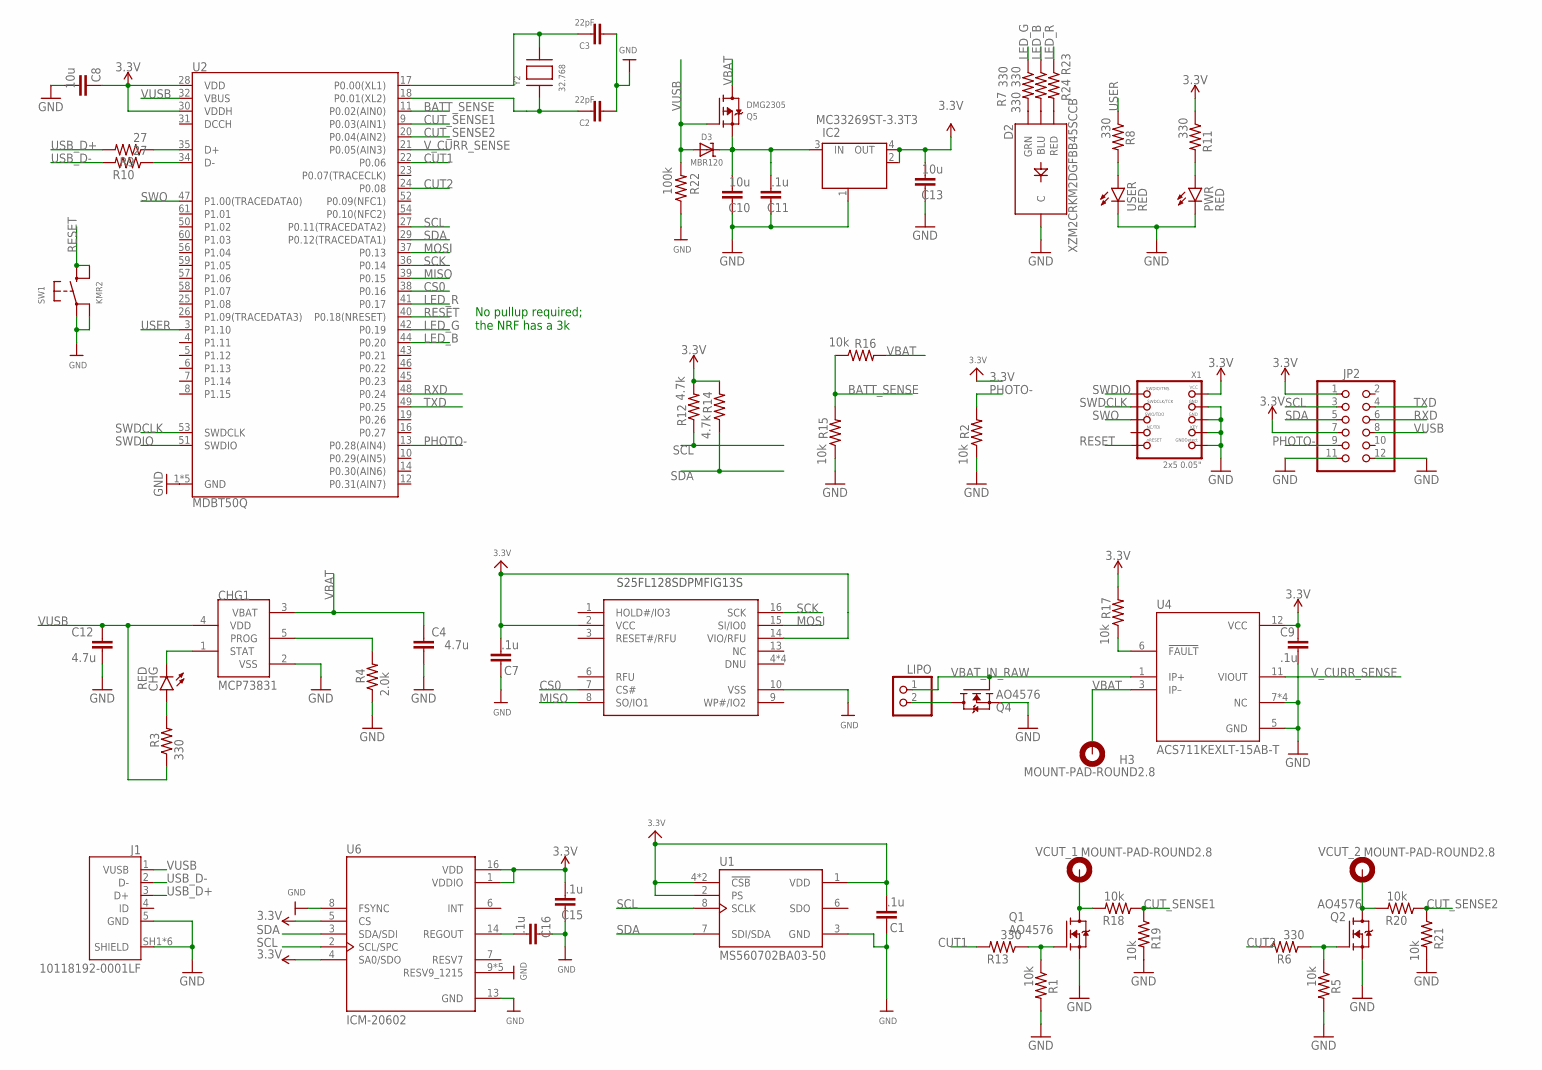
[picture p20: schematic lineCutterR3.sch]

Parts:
C1, C7, C9, C11, C15, C16: .1u; C0805
C2, C3: 22pF; C0805
C4, C12: 4.7u; C0805
C8, C10, C13: 10u; C0805
CHG: RED; CHIP-LED0805
CHG1: MCP73831; SOT23-5L
D2: XZM2CRKM2DGFBB45SCCB; PLCC4SMDLED
D3: MBR120; SOD-123
H3: MOUNT-PAD-ROUND2.8; 2,8-PAD
IC2: MC33269ST-3.3T3; SOT223
J1: 10118192-0001LF; AMPHENOL_10118192-0001LF
JP2: PINHD-2X6; 2X06
LIPO: PINHD-1X2; 1X02
PWR: RED; CHIP-LED0805
Q1, Q2, Q4: AO4576; SOIC8
Q5: DMG2305; SOT23-R
R1, R2, R5, R15, R16, R17, R18, R19, R20, R21: 10k; R0805
R3, R6, R7, R8, R11, R13, R23, R24: 330; R0805
R4: 2.0k; R0805
R9, R10: 27; R0805
R12, R14: 4.7k; R0805
R22: 100k; R0805
SW1: KMR2; BTN_KMR2_4.6X2.8
U1: MS560702BA03-50; SON125P300X500X100-8N
U2: MDBT50Q
U3: S25FL128SDPMFIG13S03016; SOIC127P1032X265-16N
U4: ACS711KEXLT-15AB-T; SENSOR_ACS711KEXLT-31AB-T
U6: ICM-20602; PQFN50P300X300X80-16N
USER: RED; CHIP-LED0805
VCUT_1, VCUT_2: MOUNT-PAD-ROUND2.8; 2,8-PAD
X1: 2x5 0.05"; 2X05_1.27MM_BOX_POSTS
Y2: 32.768; XTAL3215

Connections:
3.3V: C1.2, C7.2, C8.1, C9.1, C13.2, C15.2, IC2.2 (OUT), IC2.4 (OUT), JP2.1, JP2.7, R11.1, R12.2, R14.2, R17.2, U1.1 (VDD), U1.2 (PS), U1.4 (!CSB), U1.5 (!CSB), U2.28 (VDD), U2.30 (VDDH), U3.2 (VCC), U3.14 (VIO/RFU), U4.12 (VCC), U6.1 (VDDIO), U6.4 (SA0/SDO), U6.5 (CS), U6.16 (VDD), X1.1 (VCC)
BATT_SENSE: R15.2, R16.1, U2.11 (P0.02(AIN0))
CS0: U2.38 (P0.16), U3.7 (CS#)
CUT1: R13.2, U2.22 (P0.06)
CUT2: R6.2, U2.24 (P0.08)
CUT_SENSE1: R18.1, R19.1, U2.9 (P0.03(AIN1))
CUT_SENSE2: R20.1, R21.1, U2.20 (P0.04(AIN2))
GND: C1.1, C2.2, C3.2, C4.2, C7.1, C8.2, C9.2, C10.1, C11.1, C12.2, C13.1, C15.1, C16.1, CHG1.2 (VSS), D2.4 (C), IC2.1 (GND/ADJ), J1.5 (GND), J1.SH1 (SHIELD), J1.SH2 (SHIELD), J1.SH3 (SHIELD), J1.SH4 (SHIELD), J1.SH5 (SHIELD), J1.SH6 (SHIELD), JP2.11, JP2.12, PWR.C, Q1.P$1 (S), Q1.P$2 (S), Q1.P$3 (S), Q2.P$1 (S), Q2.P$2 (S), Q2.P$3 (S), Q4.P$1 (S), Q4.P$2 (S), Q4.P$3 (S), R1.2, R2.1, R4.1, R5.2, R15.1, R19.2, R21.2, R22.1, SW1.A, SW1.A' (P1), U1.3 (GND), U2.1 (GND), U2.2 (GND), U2.15 (GND), U2.33 (GND), U2.55 (GND), U3.10 (VSS), U4.5 (GND), U4.7 (NC), U4.8 (NC), U4.9 (NC), U4.10 (NC), U6.8 (FSYNC), U6.9 (RESV9_1215), U6.10 (RESV9_1215), U6.11 (RESV9_1215), U6.12 (RESV9_1215), U6.13 (GND), U6.15 (RESV9_1215), USER.C, X1.3 (GND), X1.5 (GND), X1.7 (KEY), X1.9 (GNDDETECT)
LED_B: R23.1, U2.44 (P0.20)
LED_G: R7.1, U2.42 (P0.19)
LED_R: R24.1, U2.41 (P0.17)
MISO: U2.39 (P0.15), U3.8 (SO/IO1)
MOSI: U2.37 (P0.13), U3.15 (SI/IO0)
unnamed: CHG.A, R3.2
unnamed: C2.1, U2.18 (P0.01(XL2)), Y2.P$1
unnamed: Q2.P$4 (G), R5.1, R6.1
unnamed: CHG1.5 (PROG), R4.2
unnamed: CHG.C, CHG1.1 (STAT)
unnamed: Q2.P$5 (D), Q2.P$6 (D), Q2.P$7 (D), Q2.P$8 (D), R20.2, VCUT_2.B2,8
unnamed: R8.2, USER.A
unnamed: LIPO.2, Q4.P$5 (D), Q4.P$6 (D), Q4.P$7 (D), Q4.P$8 (D)
unnamed: PWR.A, R11.2
unnamed: Q1.P$4 (G), R1.1, R13.1
unnamed: R9.1, U2.35 (D+)
unnamed: R10.1, U2.34 (D-)
unnamed: C3.1, U2.17 (P0.00(XL1)), Y2.P$2
unnamed: R17.1, U4.6 (!FAULT)
unnamed: D2.2 (GRN), R7.2
unnamed: D2.3 (BLU), R23.2
unnamed: Q1.P$5 (D), Q1.P$6 (D), Q1.P$7 (D), Q1.P$8 (D), R18.2, VCUT_1.B2,8
unnamed: D2.1 (RED), R24.2
unnamed: C16.2, U6.14 (REGOUT)
PHOTO-: JP2.9, R2.2, U2.13 (P0.28(AIN4))
RESET: SW1.B (S), SW1.B' (S1), U2.40 (P0.18(NRESET)), X1.10 (NRESET)
RXD: JP2.6, U2.48 (P0.24)
SCK: U2.36 (P0.14), U3.16 (SCK)
SCL: JP2.3, R12.1, U1.8 (SCLK), U2.27 (P0.11(TRACEDATA2)), U6.2 (SCL/SPC)
SDA: JP2.5, R14.1, U1.7 (SDI/SDA), U2.29 (P0.12(TRACEDATA1)), U6.3 (SDA/SDI)
SWDCLK: U2.53 (SWDCLK), X1.4 (SWDCLK)
SWDIO: U2.51 (SWDIO), X1.2 (SWDIO)
SWO: U2.47 (P1.00(TRACEDATA0)), X1.6 (SWO)
TXD: JP2.4, U2.49 (P0.25)
USB_D+: J1.3 (D+), R9.2
USB_D-: J1.2 (D-), R10.2
USER: R8.1, U2.3 (P1.10)
VBAT: C4.1, CHG1.3 (VBAT), H3.B2,8, Q5.3 (D), R16.2, U4.3 (IP–)
VBAT_IN_RAW: LIPO.1, Q4.P$4 (G), U4.1 (IP+)
VIN_REG1: C10.2, C11.2, D3.C, IC2.3 (IN), Q5.2 (S)
VUSB: C12.1, CHG1.4 (VDD), D3.A, J1.1 (VUSB), JP2.8, Q5.1 (G), R3.1, R22.2, U2.32 (VBUS)
V_CURR_SENSE: U2.21 (P0.05(AIN3)), U4.11 (VIOUT)

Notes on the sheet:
S25FL128SDPMFIG13S
No pullup required; the NRF has a 3k

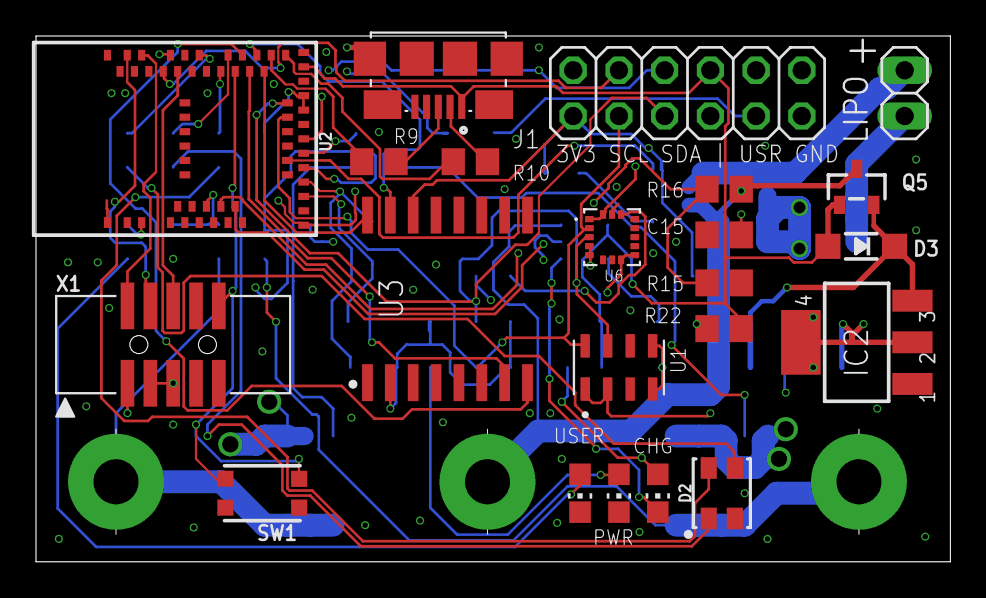
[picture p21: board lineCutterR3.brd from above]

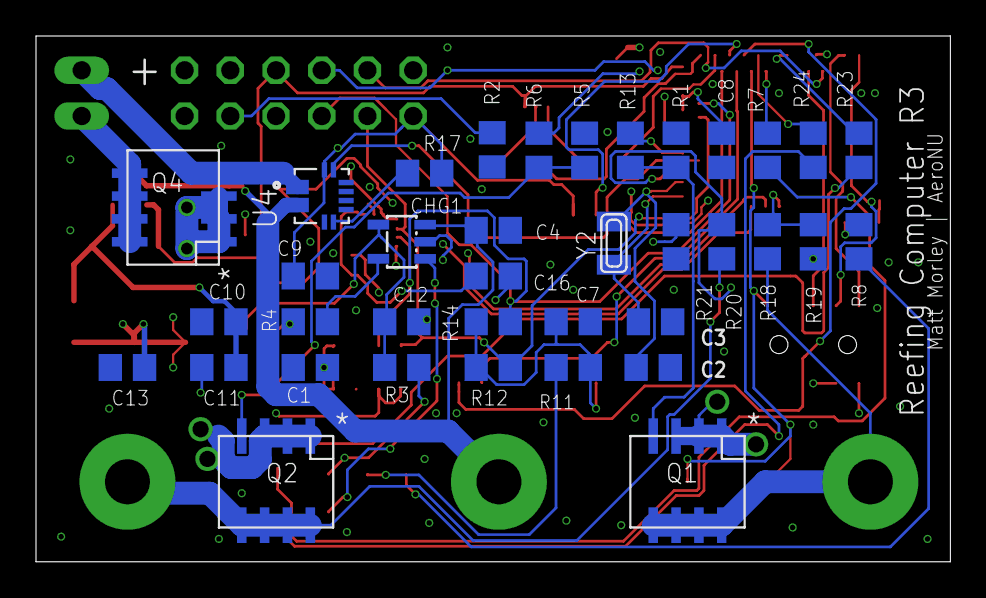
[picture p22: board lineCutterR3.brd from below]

Board: 4 copper layers, 50.8 x 29.2 mm, 62 parts (37 on the bottom side), 50 nets.

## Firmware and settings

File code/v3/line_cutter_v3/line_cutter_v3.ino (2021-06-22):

#include <Adafruit_LittleFS.h>
#include <bluefruit.h>
#include <InternalFileSystem.h>
#include <Wire.h>
#include "MovingAvg.h"
#include "MS5xxx.h"
#include "S25FL.h"
#include "icm20602/ICM20602.h"

char* boardName; // Get this from the board's ID file

enum states {
  WAITING,  // Before BLE arming
  ARMED,  // Should only be armed once on rail
  DEPLOYED,
  PARTIAL_DISREEF,  // After first line is cut
  FULL_DISREEF,  // After second line is cut
  LANDED
};
int state = WAITING;
char* stateStrings[6] = { "WAITING", "ARMED", "DEPLOYED", "PARTIAL_DISREEF", "FULL_DISREEF", "LANDED" };

// Pins
const int VOLTAGE_DIVIDER = A4;
const int NICHROME_PIN1 =   11;
const int NICHROME_PIN2 =   12;
const int PHOTO_PIN =       A3;
const int CALIBRATION_LED = PIN_LED2;
const int CUT_SENSE1 =      A5;
const int CUT_SENSE2 =      A0;
const int CURRENT_SENSE =   A1;
const int CHIP_SELECT_PIN = 8;
// We can only add ONE pin per HardwarePWM; adding more makes them randomly flash
HardwarePWM& hardwarePWM1 = HwPWM0;
HardwarePWM& hardwarePWM2 = HwPWM1;

// Barometer and moving averages
MS5xxx baro(&Wire);
int ARRAY_SIZE = 40;  // 2 seconds at 20Hz
MovingAvg altitudeReadings(ARRAY_SIZE);  // Store recent altitude readings
MovingAvg altitudeAvgDeltas(ARRAY_SIZE);  // Store differences between avgs calculated using ^
// Altitude calculation
double seaLevel;

// For logging data in internal filesystem and flash
using namespace Adafruit_LittleFS_Namespace;
const char* STATE_FILE = "stateChangeLog.txt";
const char* ID_FILE = "ID.txt";
const char* FLIGHT_VARIABLE_FILE = "flightVariables.txt";
File file(InternalFS);
S25FL flash(CHIP_SELECT_PIN);  // Starts Flash class and initializes SPI
unsigned long flashLocation;  // Next location to write data to
unsigned long flashLocationLocation;  // Next location to write flash location to
uint8_t metadata[64];
uint8_t sectorPortion[4096];

// Variables used in loop()
const int DELAY = 50;  // milliseconds
unsigned long loopStart = 0;
unsigned long lastStateChange = 0;
unsigned long lastDark = 0; // Last time it was below LIGHT_THRESHHOLD
unsigned long cutStart1 = 0;
unsigned long cutStart2 = 0;
bool armed = false;
int32_t pressure;  // pascals
double altitude;  // meters
double previousAltitudeAvg;
double currentAltitudeAvg;
double delta;  // meters/second
double currentDeltaAvg;
int light;

// bluetooth magic
// OTA DFU service
BLEDfu bledfu;
// Uart over BLE service
BLEUart bleuart;
// Function prototypes for packetparser.cpp
uint8_t readPacket (BLEUart *ble_uart, uint16_t timeout);
float   parsefloat (uint8_t *buffer);
void    printHex   (const uint8_t * data, const uint32_t numBytes);
// Packet buffer
extern uint8_t packetbuffer[];

IMU imu{}; // accelerometer
imu_out_t accelData;

// For writing data to flash & state transition log
struct Data {
  uint8_t structType = 0;  // data struct
  uint8_t state;
  uint32_t timestamp;
  uint32_t pressure;
  float altitude;
  float avgAltitude;
  float deltaAltitude;
  float avgDeltaAltitude;
  float temperature;
  float accelX;
  float accelY;
  float accelZ;
  uint16_t battSense;
  uint16_t cutSense1;
  uint16_t cutSense2;
  uint16_t currentSense;
  uint16_t photoresistor;
};
Data currentData;
const int DATA_SIZE = sizeof(Data);

// For writing data to flash & flight variable log
struct FlightVariables {
  uint8_t structType = 1;  // flight variable struct
  float limitVel;
  uint16_t altitude1;
  uint16_t altitude2;
  uint32_t disreefDelay1;
  uint32_t disreefDelay2;
  float pwmVoltage1;
  float pwmVoltage2;
  uint16_t pwmDuration;
  uint16_t lightThreshold;
  uint32_t lightTriggerTime;
  uint32_t seaLevelPressure;
};
FlightVariables currentFlightVars;
const int FLIGHT_VARIABLE_SIZE = sizeof(FlightVariables);

/*****************************
          SETUP/LOOP
 ****************************/

void setup() {
  // Manually add nichrome pins to HardwarePWMs and set them
  hardwarePWM1.setResolution(8);  // Write values in range [0, 255]
  hardwarePWM1.addPin(NICHROME_PIN1);
  hardwarePWM1.writePin(NICHROME_PIN1, 0);
  hardwarePWM2.setResolution(8);  // Write values in range [0, 255]
  hardwarePWM2.addPin(NICHROME_PIN2);
  hardwarePWM2.writePin(NICHROME_PIN2, 0);
  analogReadResolution(10);  // Read values in range [0, 1023]

  Serial.begin(115200);
  /*while (!Serial) {
    delay(10);
  }*/

  Wire.begin();
  // Connect to accelerometer
  while (!imu.begin()) {
    Serial.println("Error connecting to accelerometer...");
  }
  // Connect to barometer
  while ( baro.connect() > 0 ) {
    Serial.println("Error connecting to barometer...");
    delay(500);
  }
  // Calibrate barometer and get initial reading
  baro.ReadProm();
  baro.Readout();

  // Initialize moving averages
  seaLevel = calibrateSeaLevel(50);
  Serial.print("Sea level pressure [Pa]: ");
  Serial.println(seaLevel);
  altitudeReadings.begin();
  altitudeReadings.reading(pressureToAltitude(baro.GetPres()));
  altitudeAvgDeltas.begin();
  altitudeAvgDeltas.reading(0.0);

  // Initialize Internal File System
  if (InternalFS.begin()) {
    Serial.println("FS initialized.");
  } else {
    Serial.println("Could not start file system.");
  }

  // Get identifier info (board version and Bluetooth name)
  file.open(ID_FILE, FILE_O_READ);
  uint32_t readlen;
  char buffer[64] = { 0 };
  readlen = file.read(buffer, sizeof(buffer));
  buffer[readlen] = 0;
  file.close();
  boardName = buffer;
  Serial.print("Board: ");
  Serial.println(boardName);

  // Set up flash
  SPI.begin();
  SPI.setBitOrder(MSBFIRST);
  SPI.setClockDivider(SPI_CLOCK_DIV8);  // Divide the clock by 8
  SPI.setDataMode(SPI_MODE0);
  pinMode(CHIP_SELECT_PIN, OUTPUT);
  digitalWrite(CHIP_SELECT_PIN, HIGH);

  // Set up BLE
  Bluefruit.begin(2, 0);
  Bluefruit.setTxPower(8);    // Check bluefruit.h for supported values
  Bluefruit.setName(boardName);
  // To be consistent OTA DFU should be added first if it exists
  bledfu.begin();
  // Configure and start the BLE Uart service
  bleuart.begin();
  // Set up and start advertising
  startAdv();
  Serial.println("Started advertising.");

  setFlashLocation();
  readFlightVariables();
  updateFlash(( uint8_t* ) &currentFlightVars, FLIGHT_VARIABLE_SIZE);
}


void loop() {
  while (millis() < loopStart + DELAY) {}

  loopStart = millis();  // Used for timestamps in data log

  // Read pressure, calculate altitude
  baro.Readout();
  pressure = baro.GetPres();
  altitude = pressureToAltitude(pressure);

  // Update moving averages
  previousAltitudeAvg = altitudeReadings.getAvg();
  currentAltitudeAvg = altitudeReadings.reading(altitude);  // Update and return new avg
  delta = (currentAltitudeAvg - previousAltitudeAvg) * (1000.0 / DELAY);
  currentDeltaAvg = altitudeAvgDeltas.reading(delta);  // Update and return new avg

  // Update photoresistor
  light = analogRead(PHOTO_PIN);
  // Keep track of whether it is dark or light and for how long
  if (light < currentFlightVars.lightThreshold)
    lastDark = loopStart;

  // Update accelerometer
  accelData = imu.readout();

  // Update data struct, send to BLE central and flash
  updateDataStruct();
  updateFlash(( uint8_t* ) &currentData, DATA_SIZE);

  while (bleuart.available()) {
    uint8_t ch;
    ch = (uint8_t) bleuart.read();
    // '!' indicates start of a command. anything else is ignored
    if (ch == (uint8_t) '!') {
      parse_command();
    }
  }

  if (cutStart1 > 0 && loopStart - cutStart1 > currentFlightVars.pwmDuration) {
    hardwarePWM1.writePin(NICHROME_PIN1, 0);
    Serial.print("Ended PWM on pin ");
    Serial.println(NICHROME_PIN1);
  }
  if (cutStart2 > 0 && loopStart - cutStart2 > currentFlightVars.pwmDuration) {
    hardwarePWM2.writePin(NICHROME_PIN2, 0);
    Serial.print("Ended PWM on pin ");
    Serial.println(NICHROME_PIN2);
  }

  switch (state) {
    case WAITING:
      if (armed == true) {
        state = ARMED;
      }
      break;
    case ARMED:
      if (armed == false) {
        state = WAITING;
      }
      if (loopStart - lastDark > currentFlightVars.lightTriggerTime) {
        InternalFS.remove(STATE_FILE);
        progressState();
      }
      break;
    case DEPLOYED:
      if (currentAltitudeAvg < currentFlightVars.altitude1
          || loopStart - lastStateChange > currentFlightVars.disreefDelay1) {
        pwmStart();
        cutStart1 = loopStart;
        progressState();
      }
      break;
    case PARTIAL_DISREEF:
      if (currentAltitudeAvg < currentFlightVars.altitude2
          || loopStart - lastStateChange > currentFlightVars.disreefDelay2) {
        pwmStart();
        cutStart2 = loopStart;
        progressState();
      }
      break;
    case FULL_DISREEF:
      if (abs(currentDeltaAvg) < 0.05) {
        progressState();
      }
      break;
    case LANDED:
      // Nothing happens after landing
      break;
    default:
      Serial.println("Something has gone horribly wrong if none of the states match.");
  }
}


/*****************************
            HELPERS
 ****************************/

void parse_command() {
  uint8_t char_array[8];
  int current_num = 0;

  // read text after '!' which started command
  while ( bleuart.available() && current_num < 8 )
  {
    char_array[current_num] = (uint8_t) bleuart.read();
    current_num++;
  }

  String command = (char*) char_array;

  // if user typed '!cut', execute line-cutting
  if (command.substring(0, 4).equals("help")) {
    bleuart.print("Valid commands:\n");
    bleuart.print("!arm\n");
    bleuart.print("!disarm\n");
    bleuart.print("!vars\n");
    bleuart.print("!data\n");
  }
  else if (command.substring(0, 3).equals("arm")) {
    if (state == WAITING) {
      armed = true;
      bleuart.print("Armed.\n");
    } else {
      bleuart.print("Not in waiting state.\n");
    }
  }
  else if (command.substring(0, 6).equals("disarm")) {
    if (state == ARMED) {
      armed = false;
      bleuart.print("Disarmed.\n");
    } else {
      bleuart.print("Not in armed state.\n");
    }
  }
  else if (command.substring(0, 4).equals("vars")) {
    sendFlightVariables();
  }
  else if (command.substring(0, 4).equals("data")) {
    sendSensorData();
  }
  else {
    bleuart.print("Not a valid command.\n");
    return;
  }
}

void startAdv(void)
{
  // Advertising packet
  Bluefruit.Advertising.addFlags(BLE_GAP_ADV_FLAGS_LE_ONLY_GENERAL_DISC_MODE);
  Bluefruit.Advertising.addTxPower();

  // Include the BLE UART (AKA 'NUS') 128-bit UUID
  Bluefruit.Advertising.addService(bleuart);

  // Secondary Scan Response packet (optional)
  // Since there is no room for 'Name' in Advertising packet
  Bluefruit.ScanResponse.addName();

  /* Start Advertising
     - Enable auto advertising if disconnected
     - Interval:  fast mode = 20 ms, slow mode = 152.5 ms
     - Timeout for fast mode is 30 seconds
     - Start(timeout) with timeout = 0 will advertise forever (until connected)

     For recommended advertising interval
     https://developer.apple.com/library/content/qa/qa1931/_index.html
  */
  Bluefruit.Advertising.restartOnDisconnect(true);
  Bluefruit.Advertising.setInterval(32, 244);    // in unit of 0.625 ms
  Bluefruit.Advertising.setFastTimeout(30);      // number of seconds in fast mode
  Bluefruit.Advertising.start(0);                // 0 = Don't stop advertising after n seconds
}

void setFlashLocation() {
  Serial.println("Setting flash location... ");
  flash.read_start(0, metadata, 64);
  flashLocationLocation = 1;
  if (metadata[0] == 0) {  // If it wasn't bulk erased recently
    while (flashLocationLocation < 64 && metadata[flashLocationLocation] == 0) {
      flashLocationLocation++;
    }
    Serial.print("Flash is not empty, ");
    Serial.print(flashLocationLocation - 2);  // Subtract extra 1 because 1 sector is metadata
    Serial.println("/63 flight data sectors full.");

    flashLocation = (flashLocationLocation - 1) * 0x40000;  // Go to start of last non-empty sector
    // Linear search
    bool foundLocation = false;
    int i = 0;
    while (!foundLocation && i < 0x40000) {
      if (i % 4096 == 0) {  // Read large blocks at a time
        flash.read_start(flashLocation + i, sectorPortion, 4096);
      }
      foundLocation = (sectorPortion[i % 4096] == 0xff);  // Access the first byte of the struct
      i += 64;
    }
    flashLocation = flashLocation + i - 64;  // It overshoots by one position
  } else {
    Serial.println("Flash is empty, writing metadata.");
    uint8_t temp = 0;
    flash.write(0, &temp, 1); // Indicate that there is data in the metadata sector
    flashLocation = 0x40000;
  }
  Serial.print("Next flash write in sector ");
  Serial.print(flashLocation / 0x40000);
  Serial.print(" at position ");
  Serial.print(flashLocation % 0x40000);
  Serial.println(".");
}

// Get variables for this flight from InternalFS
void readFlightVariables() {
  if (file.open(FLIGHT_VARIABLE_FILE, FILE_O_READ)) {
    uint8_t buff[64] = {0};
    file.read(buff, FLIGHT_VARIABLE_SIZE);
    currentFlightVars = *( FlightVariables* ) &buff;
    currentFlightVars.seaLevelPressure = seaLevel;
    Serial.println("Finished reading flight variables.");
  } else {
    Serial.println("Failed to read flight variables.");
  }
}

// Average several readings to get "sea level" pressure
double calibrateSeaLevel(int samples) {
  Serial.print("Reading current pressure... ");
  digitalWrite(CALIBRATION_LED, HIGH);
  int sum = 0;
  for (int i = 0; i < samples; i++) {
    baro.Readout();
    sum += baro.GetPres();
    delay(100);
  }
  Serial.println("Done.");
  digitalWrite(CALIBRATION_LED, LOW);
  return sum / (double) samples;
  Serial.println("Done");
}

// Convert pressure (in pascals) to altitude (in meters) using sea level pressure
double pressureToAltitude(int32_t pressure) {
  return 44330.76 * (1.0 - pow(pressure / seaLevel, 1.0 / 5.25588));
}

// PWM pin to heat nichrome and cut parachute line
void pwmStart() {
  int level;
  Serial.print("Starting PWM on pin ");
  if (state == DEPLOYED) {
    Serial.print(NICHROME_PIN1);
    level = pwmLevel(currentFlightVars.pwmVoltage1);
    hardwarePWM1.writePin(NICHROME_PIN1, level);
  } else if (state == PARTIAL_DISREEF) {
    Serial.print(NICHROME_PIN2);
    level = pwmLevel(currentFlightVars.pwmVoltage2);
    hardwarePWM2.writePin(NICHROME_PIN2, level);
  }
  Serial.print(" with level ");
  Serial.println(level);
}

// Calculate number to be used for PWM of nichrome pin
int pwmLevel(double targetVoltage) {
  int vbatAnalog = 2 * analogRead(VOLTAGE_DIVIDER);
  // Analog reading is out of 1023, so divide and then multiply by 3.6 (reference voltage)
  double vbat =  3.6 * (vbatAnalog / 1023.0);
  // Find proportion of vbat needed to apply target voltage, then make out of 255 for analog write
  return (targetVoltage / vbat) * 255;
}

void progressState() {
  Serial.print(state);
  Serial.print(" -> ");
  Serial.println(state + 1);
  Serial.println(loopStart);
  writeStateChangeData();
  lastStateChange = loopStart;
  state++;
}

void writeStateChangeData() {
  if ( file.open(STATE_FILE, FILE_O_WRITE) ) {
    uint8_t* buffer = ( uint8_t* ) &currentData;

    Serial.print("Writing data to file... ");
    file.write(state);
    file.write(" -> ");
    file.write(state + 1);
    file.write(buffer, DATA_SIZE);
    file.close();
    Serial.println("Done");
  } else {
    Serial.print("Failed to write ");
    Serial.println(STATE_FILE);
  }
}

void updateDataStruct() {
  currentData.state = state;
  currentData.timestamp = loopStart;
  currentData.pressure = pressure;
  currentData.altitude = altitude;
  currentData.avgAltitude = currentAltitudeAvg;
  currentData.deltaAltitude = altitude;
  currentData.avgDeltaAltitude = currentDeltaAvg;
  currentData.temperature = baro.GetTemp();
  currentData.accelX = accelData.accel_xout;
  currentData.accelY = accelData.accel_yout;
  currentData.accelZ = accelData.accel_zout;
  currentData.battSense = analogRead(VOLTAGE_DIVIDER);
  currentData.cutSense1 = analogRead(CUT_SENSE1);
  currentData.cutSense2 = analogRead(CUT_SENSE2);
  currentData.currentSense = analogRead(CURRENT_SENSE);
  currentData.photoresistor = light;
}

void sendSensorData() {
  bleuart.printf("State [%i]\n", currentData.state);
  bleuart.printf("Time [%i]\n", currentData.timestamp);
  bleuart.printf("Press [%u Pa]\n", currentData.pressure);
  bleuart.printf("Temp [%f C]\n", currentData.temperature);
  bleuart.printf("Ax [%f]\n", currentData.accelX);
  bleuart.printf("Ay [%f]\n", currentData.accelY);
  bleuart.printf("Az [%f]\n", currentData.accelZ);
  bleuart.printf("Batt [%f]\n", currentData.battSense * 2.0 * 3.6 / 1023.0);
  bleuart.printf("CutSens1 [%li]\n", currentData.cutSense1);
  bleuart.printf("CutSens2 [%li]\n", currentData.cutSense2);
  bleuart.printf("CurrSens [%li]\n", currentData.currentSense);
  bleuart.printf("Photores [%li]\n", currentData.photoresistor);
}

void sendFlightVariables() {
  bleuart.printf("Cut1Alt [%u m]\n", currentFlightVars.altitude1);
  bleuart.printf("Cut2Alt [%u m]\n", currentFlightVars.altitude2);
  bleuart.printf("Cut1Time [%u ms]\n", currentFlightVars.disreefDelay1);
  bleuart.printf("Cut2Time [%u ms]\n", currentFlightVars.disreefDelay2);
  bleuart.printf("VoltPWM1 [%f V]\n", currentFlightVars.pwmVoltage1);
  bleuart.printf("VoltPWM2 [%f V]\n", currentFlightVars.pwmVoltage2);
  bleuart.printf("TimePWM [%u ms]\n", currentFlightVars.pwmDuration);
  bleuart.printf("LightThreshold [%u]\n", currentFlightVars.lightThreshold);
  bleuart.printf("LightTime [%u ms]\n", currentFlightVars.lightTriggerTime);
  bleuart.printf("SeaLevel [%u Pa]\n", currentFlightVars.seaLevelPressure);
}

void updateFlash(uint8_t* data, int sizeOfData) {
  if (flashLocation < 0x1000000) {
    // If flashLocation moves into a new sector, update meta location
    if (flashLocation % 0x40000 == 0) {
      uint8_t temp = 0;
      flash.write(flashLocationLocation, &temp, 1);
      flashLocationLocation++;
    }

    // Write things, increment location
    flash.write(flashLocation, data, sizeOfData);
    flashLocation += 64;
  }
}

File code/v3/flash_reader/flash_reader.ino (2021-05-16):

#include <SPI.h>
#include "S25FL.h"

int readMode = 0;  // set to 0 to read flight data entries, 1 to read flight variable entries
S25FL flash;  // Starts Flash class and initializes SPI
unsigned long flashLocation = 0x40000;
uint8_t metadata[64];
uint8_t sectorPortion[4096];
bool done = false;

struct Data {
  uint8_t structType = 0;  // data struct
  uint8_t state; // 1
  uint32_t timestamp; // 2
  uint32_t pressure; // 6
  float altitude; // 10
  float avgAltitude; // 14
  float deltaAltitude; // 18
  float avgDeltaAltitude; // 22
  float temperature; // 26
  float accelX; // 30
  float accelY; // 34
  float accelZ; // 38
  uint16_t battSense; // 42
  uint16_t cutSense1; // 44
  uint16_t cutSense2; // 46
  uint16_t currentSense; // 48
  uint16_t photoresistor; // 50 (ends at 52)
};
Data currentData;

// For writing data to flash & flight variable log
struct FlightVariables {
  uint8_t structType = 1;  // flight variable struct
  float limitVel;
  uint16_t altitude1;
  uint16_t altitude2;
  uint32_t disreefDelay1;
  uint32_t disreefDelay2;
  float pwmVoltage1;
  float pwmVoltage2;
  uint16_t pwmDuration;
  uint16_t lightThreshold;
  uint32_t lightTriggerTime;
  uint32_t seaLevelPressure;
};
FlightVariables currentFlightVars;

void setup() {
  Serial.begin(115200);
  while (!Serial) {
    delay(10);
  }

  SPI.begin();
  SPI.setBitOrder(MSBFIRST);
  SPI.setClockDivider(SPI_CLOCK_DIV8); // Divide the clock by 8
  SPI.setDataMode(SPI_MODE0);
  pinMode(8, OUTPUT);
  digitalWrite(8, HIGH);

  Serial.println("Metadata: ");
  flash.read_start(0, metadata, 64);
  Serial.print("[");
  for (int i = 0; i < 64; i++) {
    if (i % 8 == 0 && i > 0) {
      Serial.println();
    }
    Serial.print(metadata[i], HEX);
    if (i < 63) {
      Serial.print(",\t");
    }
  }
  Serial.println("]");
  Serial.println();
  delay(10000);  // Give time to connect with CoolTerm or similar

  while (!done) {
    if (flashLocation % 4096 == 0) {
      flash.read_start(flashLocation, sectorPortion, 4096);
    }
    if (sectorPortion[flashLocation % 4096] == readMode) {
      readData(&sectorPortion[flashLocation % 4096]);
      print_flash_packet();
    } else if (sectorPortion[flashLocation % 4096] == 0xff || flashLocation >= 0x1000000) {
      done = true;
    }
    flashLocation += 64;
  }
  delay(1);
}

void loop() {
}

void readData(uint8_t* flashData) {
  if (readMode == 0) {
    currentData = *( Data* ) flashData;
  } else {
    currentFlightVars = *( FlightVariables* ) flashData;
  }
}

void print_flash_packet() {
  if (readMode == 0) {
    Serial.printf("%u,%u,%u,%f,%f,%f,%f,%f,%f,%f,%f,%u,%u,%u,%u,%li\n",
                  currentData.state, currentData.timestamp, currentData.pressure,
                  currentData.altitude, currentData.avgAltitude, currentData.deltaAltitude, currentData.avgDeltaAltitude,
                  currentData.temperature, currentData.accelX, currentData.accelY, currentData.accelZ,
                  currentData.battSense, currentData.cutSense1, currentData.cutSense2,
                  currentData.currentSense, currentData.photoresistor);
  } else {
    Serial.printf("%f,%u,%u,%u,%u,%f,%f,%u,%u,%u,%u\n",
                  currentFlightVars.limitVel, currentFlightVars.altitude1, currentFlightVars.altitude2,
                  currentFlightVars.disreefDelay1, currentFlightVars.disreefDelay2,
                  currentFlightVars.pwmVoltage1, currentFlightVars.pwmVoltage2, currentFlightVars.pwmDuration,
                  currentFlightVars.lightThreshold, currentFlightVars.lightTriggerTime, currentFlightVars.seaLevelPressure);
  }
}

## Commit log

2021-02-14 Actually print pressure
2021-02-15 implemented new PWM and barometer
2021-02-17 Create i2c test code for esp32s2
    [partitions_example.csv]
2021-02-17 Print time as well as line
    Not sure how helpful this will be -- bleuart seems to have a ton of lag
2021-02-17 Start on line cutter r3 hardware
    [lineCutterR3.brd, lineCutterR3.sch]
2021-02-18 add ble, sealevel calibration w/ led
2021-02-18 longer sea level sample
2021-02-23 Add esp32 test code for MS5607 and Melon driver
2021-02-25 Add bluetooth to esp32-baro-test
2021-02-25 Add Buck/Boost, RGB, Continuity, current sense
    [lineCutterR3.brd, lineCutterR3.sch]
2021-02-28 final code for cert rocket tests
    [lineCutterR3.brd]
2021-02-28 R3 PCB: Place most of the components
    [lineCutterR3.brd, lineCutterR3.sch]
2021-02-28 Fix variable typing in line-cutter-nrf
    [line_cutter_nrf.ino]
2021-02-28 Manually interact with HardwarePWM
    It's still being stupid, but in a way that doesn't seem to fail for us.
    [line_cutter_trd.ino]
2021-03-01 Pass 1 at routing line cutter R3
    [lineCutterR3.brd, lineCutterR3.sch]
2021-03-02 pwm resolution -> 8, renamed car test code folder
2021-03-03 Switch back to 3v3 lin reg
    [lineCutterR3.brd, lineCutterR3.sch]
2021-03-03 line cutter v1 code to be preserved for all eternity
    [partitions_example.csv]
2021-03-04 Final board stuff
    [lineCutterR3.brd, lineCutterR3.sch]
2021-03-08 Move stuff into a Project
    [lineCutterR1.brd, lineCutterR1.sch, lineCutterR2.brd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]
2021-03-08 Create perfboard Eagle CAD
    Turns out CADing stuff helps
    [perfboard r2.brd, perfboard r2.sch]
2021-03-08 Fix perfboard wiring
    No, A2 isnt supposed to drive PWM too -><-
    [perfboard r2.brd, perfboard r2.sch]
2021-03-09 Reorg perfboard
    [perfboard r2.brd, perfboard r2.sch]
2021-03-09 Rename to LineCutterMemes
    [lineCutterR1.brd, lineCutterR1.sch, lineCutterR2.brd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]
2021-03-14 Add driver notes
2021-03-14 Fix photoresistor header
    Photo+ was not connected to 3v3
    [lineCutterR3.brd, lineCutterR3.sch]
2021-03-14 Update perfboard r2.brd
    [perfboard r2.brd]
2021-03-17 o r g a n i z a t i o n
    [partitions_example.csv]
2021-03-17 Add ICM20602 driver
    Fullscale is kinda bjork
2021-03-18 Document board names
2021-03-19 Add S25Fl driver ported from stm32-avionics
2021-03-20 Add accelerometer
2021-03-20 amesbury data
    [Cherry_flash.csv, DarthPlagueis_flash.csv, Strawberry_flash.csv]
2021-03-23 updated amesbury flight logs with complete data
    [Cherry_flash.csv, DarthPlagueis_flash.csv, Strawberry_flash.csv]
2021-03-29 flight data analysis
    [Strawberry_flash.csv]
2021-03-30 updated flight summary
    [Strawberry_flash.csv]
2021-03-30 including libraries that it didn't need before??
    [S25FL.h, line_cutter_v3.ino]
2021-03-30 Fix flash compilation errors
    [S25FL.cpp, S25FL.h, line_cutter_v3.ino]
2021-03-31 simplification and separate PWM process
2021-04-04 removed wire begin from ms5xxx
2021-04-11 this code is broken
    [bulk_erase.ino, identifier.ino, line_cutter_v3.ino]
2021-04-12 ready to reset IDs
    [identifier.ino]
2021-04-12 prints time taken to bulk erase
2021-04-12 Add README for schematic folder
2021-04-12 LineCutterMemes -> LineCutter
    [lineCutterR1.brd, lineCutterR1.sch, lineCutterR2.brd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]
2021-04-16 add openocd config files
    [bcm-nrf.cfg]
2021-04-19 read metadata and correct struct
    [flash_reader.ino]
2021-04-24 fixed incorrect size for flash writes
    [line_cutter_v3.ino]
2021-05-08 Add data from 5/7 drone test
    [drone_test_1_apple.csv, drone_test_1_darthplagueis.csv, drone_test_2_apple.csv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]
2021-05-16 added TCC launch data
    [pcb3_darthplagueis_flightvars.csv, pcb4_apple_flightdata.csv, pcb4_apple_flightvars.csv]
2021-05-16 fixed flash read formatting
    [flash_reader.ino]
2021-05-16 St Albans flight analyis
    [2021-05-15_SpruceGooseCherryVars.csv, 2021-05-15_SpruceGooseStrawberryVars.csv]
2021-06-30 trd flight summary graphs
    [Cherry_Flight_Vars.xlsx, Strawberry_Flight_Vars.xlsx]

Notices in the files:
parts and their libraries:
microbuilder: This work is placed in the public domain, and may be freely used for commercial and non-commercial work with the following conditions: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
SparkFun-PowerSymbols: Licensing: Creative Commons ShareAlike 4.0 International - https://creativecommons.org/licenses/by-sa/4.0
